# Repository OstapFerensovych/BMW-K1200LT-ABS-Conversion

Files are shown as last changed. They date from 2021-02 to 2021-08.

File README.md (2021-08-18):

# BMW K1200LT iABS to iABS gen 2 Conversion PCB and Firmware.

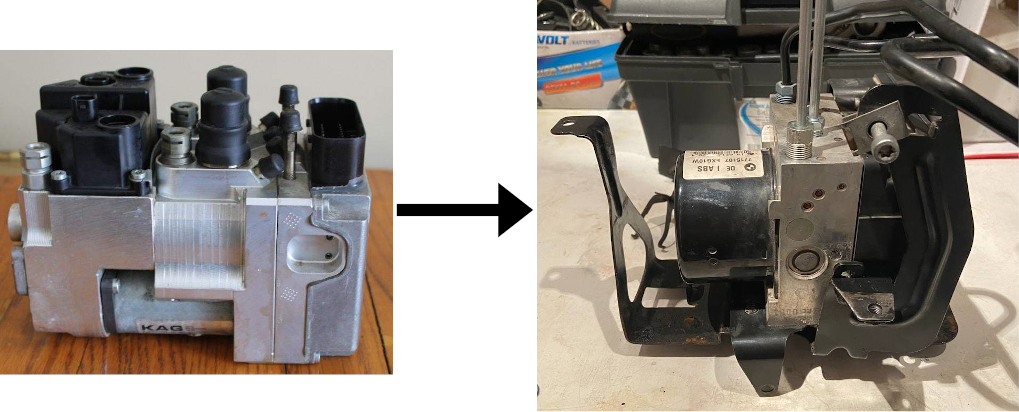
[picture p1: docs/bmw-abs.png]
BMW K1200LT ABS Conversion


To retrofit BMW K1200LT motorcycle we used the ATE/Teves iABS-II module from 2010 R1200GS K25.  
iABS-II uses CAN bus to communicate with ZFE, DME modules in the original R1200GS schematic.  

This project is developed to provide K1200LT necessary signals from ATE/Teves iABS-II CAN bus:
- Speed signal for K1200LT dash
- Brake and tail lights output
- ABS warning LED output
- General warning LED output  

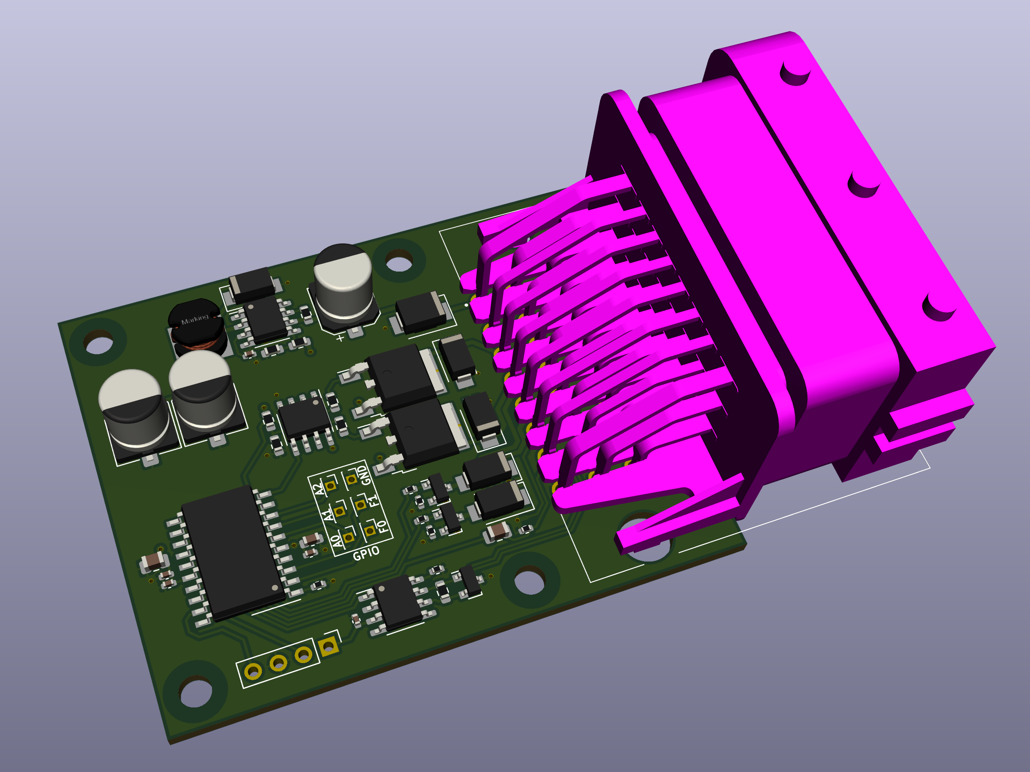
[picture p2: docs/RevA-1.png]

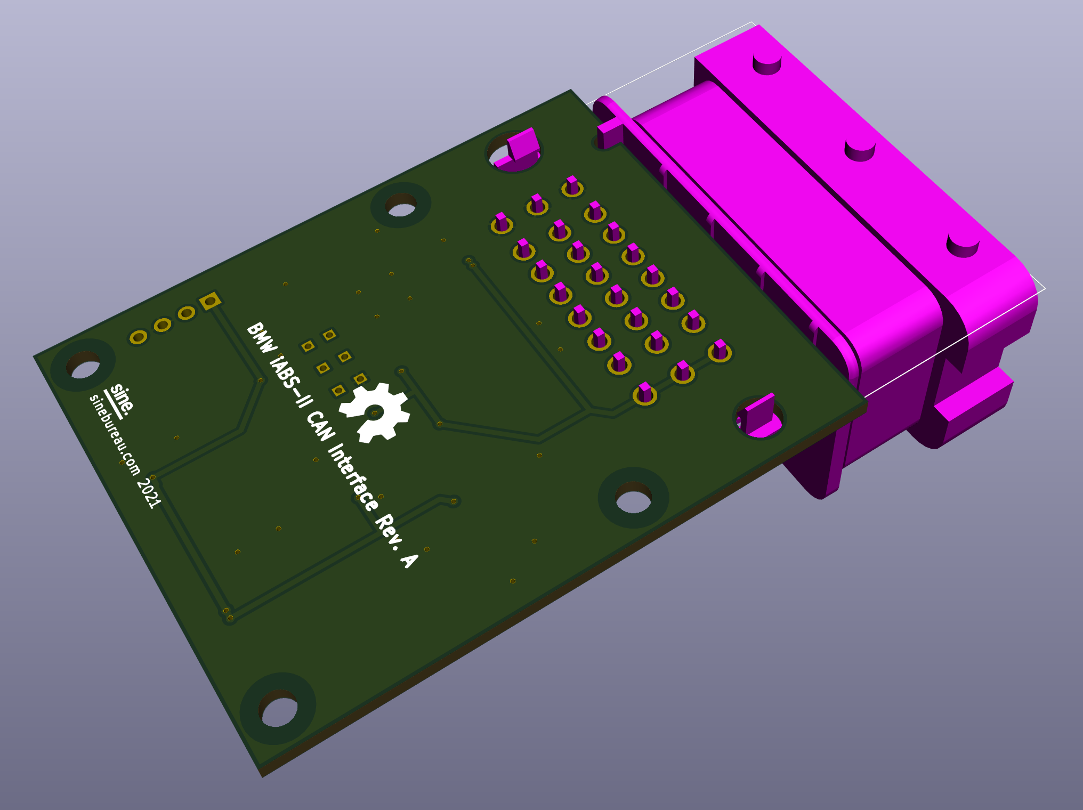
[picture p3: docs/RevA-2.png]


<!-- ![IMG_1473](https://user-images.githubusercontent.com/11366067/129911985-b8ce3c54-3990-48e8-b734-4c0b1e120d9e.jpg)
![IMG_1475](https://user-images.githubusercontent.com/11366067/129912004-15128995-6d64-4012-b580-ba468f006576.jpg)
![IMG_1476](https://user-images.githubusercontent.com/11366067/129912034-00b8ea57-16d7-4200-b9ce-d0883e993687.jpg) -->


## Other resources. 
[Shematics](docs/)

#### PCB is designed in KiCAD 5.1.9

## License

MIT

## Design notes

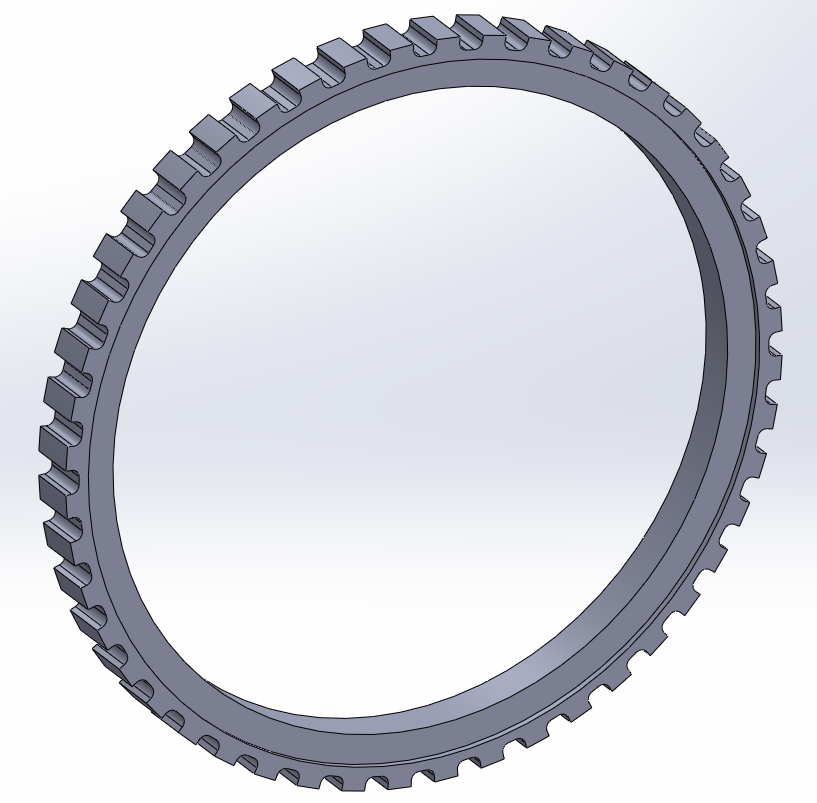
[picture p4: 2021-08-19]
docs/K1200LT_Rear_ABS_ring_48T.png

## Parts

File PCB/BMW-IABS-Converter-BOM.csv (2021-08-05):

Reference(s) | Value | Footprint | Qty | Url
C6 | 10uF | Capacitor_SMD:C_0805_2012Metric | 1
C8 | 47uF 25V | Capacitor_THT:C_Radial_D6.3mm_H11.0mm_P2.50mm | 1
C14 | 150pF | Capacitor_SMD:C_0402_1005Metric | 1 | https://www.rcscomponents.kiev.ua/product/180pf-50v-np0-5-0805-4k-reel-0805n181j500nt-hitano_54905.html
D1, D2, D3, D4 | US1M | Diode_SMD:D_SMA | 4
Q2, Q3 | IRLML0060TRPbF | Package_TO_SOT_SMD:SOT-23 | 2
R1, R7 | 200R | Resistor_SMD:R_0603_1608Metric | 2
R8, R10 | 20K | Resistor_SMD:R_0603_1608Metric | 2
R9 | 10K | Resistor_SMD:R_1206_3216Metric | 1
R11 | 2K | Resistor_SMD:R_1206_3216Metric | 1
R13 | 120R | Resistor_SMD:R_0603_1608Metric | 1
R19 | 3K 1% | Resistor_SMD:R_0603_1608Metric | 1 | https://www.rcscomponents.kiev.ua/product/3-32-kohm-1-0-125w-150v-0805-rc0805fr-3k32-hitano-rezistor-smd_27756.html
U2 | STM32F042F4Px | Package_SO:TSSOP-20_4.4x6.5mm_P0.65mm | 1
U3 | LMC662AIM | Package_SO:SOIC-8_3.9x4.9mm_P1.27mm | 1

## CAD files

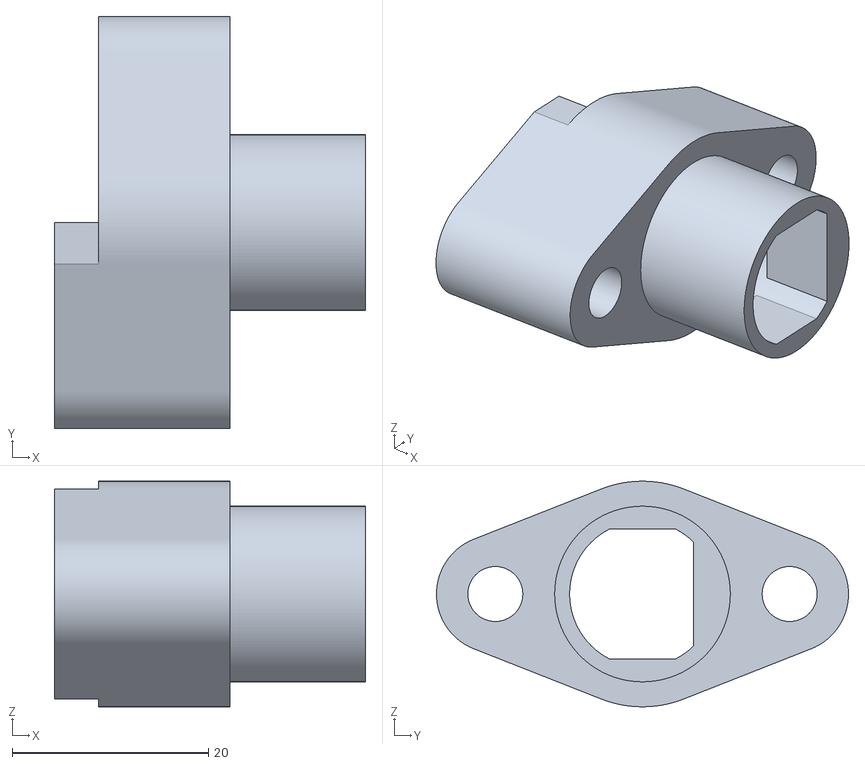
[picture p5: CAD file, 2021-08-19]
3D Files/K1200LT_ABS_Sensor_Bracket.stl
31.7 x 42.0 x 23.0

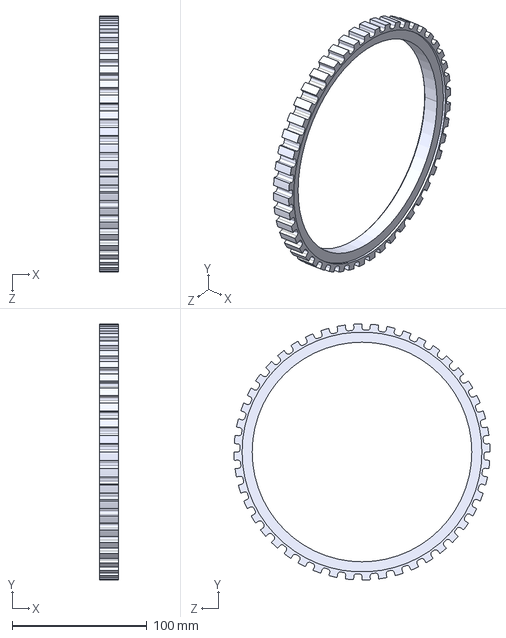
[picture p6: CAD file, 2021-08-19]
3D Files/K1200LT-Rear-ABS-Ring-48T.STEP
14.0 x 190.0 x 190.0 mm

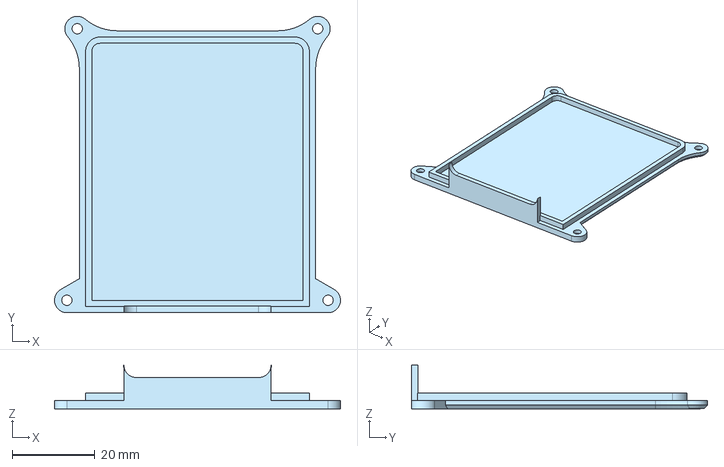
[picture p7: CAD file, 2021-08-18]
3D Files/Case-02a.step
69.0 x 71.5 x 10.6 mm

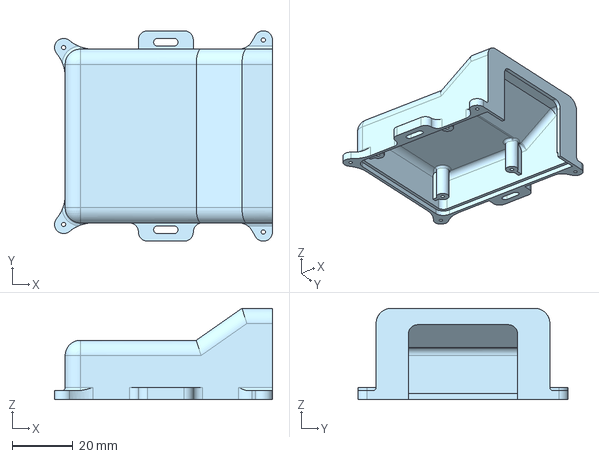
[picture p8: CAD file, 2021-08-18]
3D Files/Case-01a.step
71.5 x 69.0 x 30.0 mm

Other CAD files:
3D Files/Case-02a.stl

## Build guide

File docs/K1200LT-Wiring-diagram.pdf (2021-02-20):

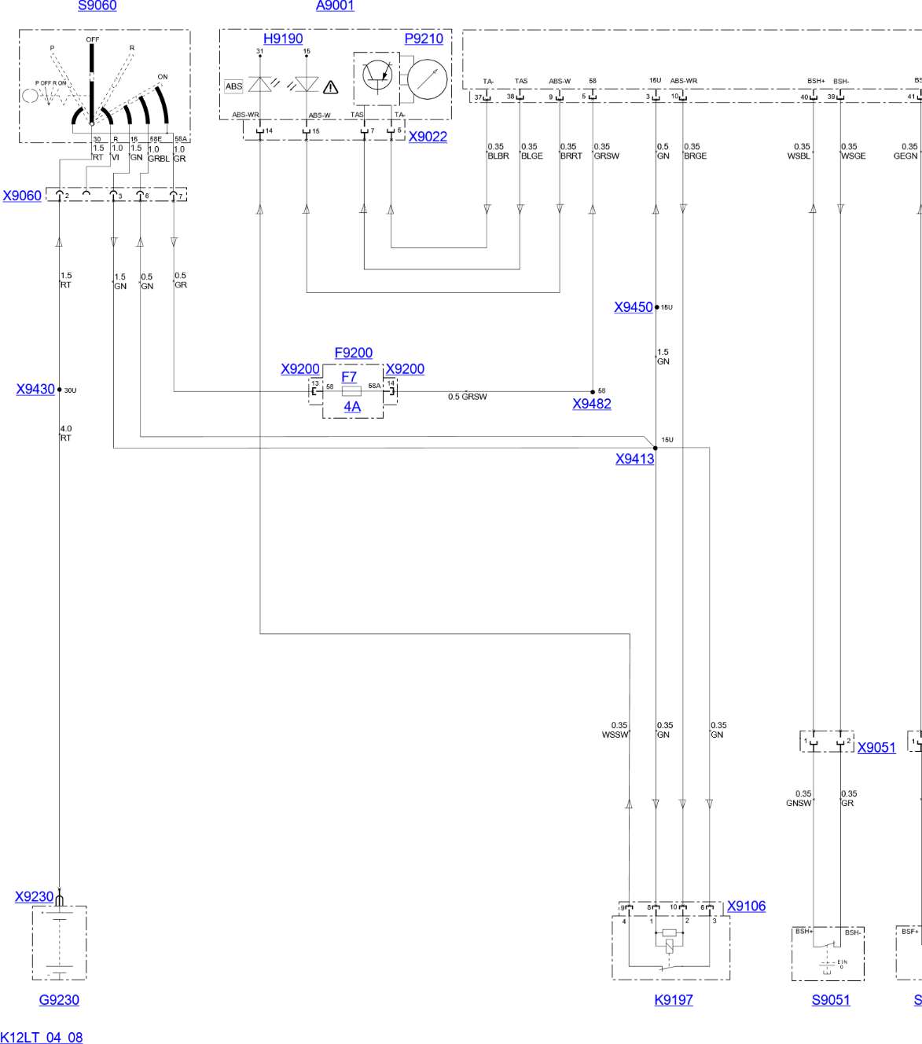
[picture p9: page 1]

SSP-SSP-BIKE_K12LT_04_08 BIKE_K12LT_04_08 | 1/3

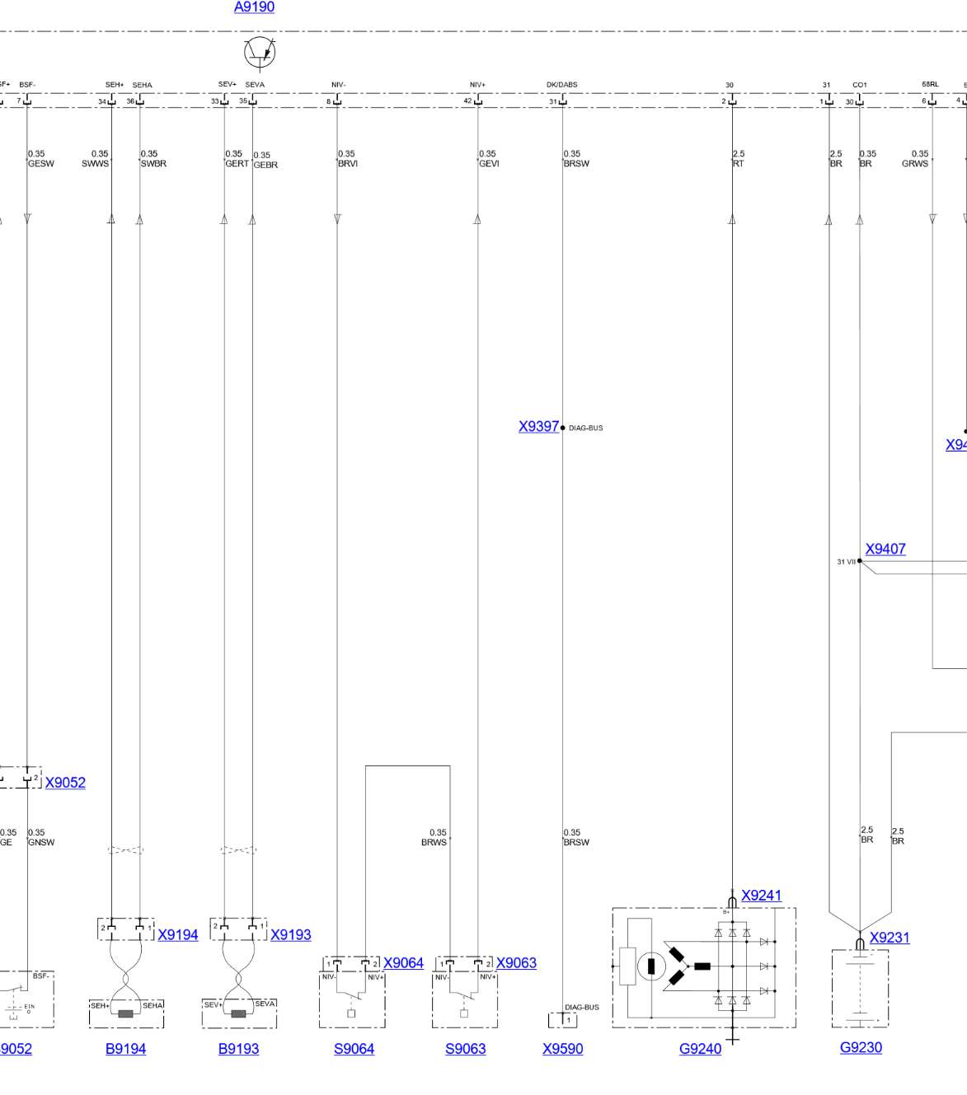
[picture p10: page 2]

SSP-SSP-BIKE_K12LT_04_08 BIKE_K12LT_04_08 | 2/3

SSP-SSP-BIKE_K12LT_04_08 BIKE_K12LT_04_08 | 3/3

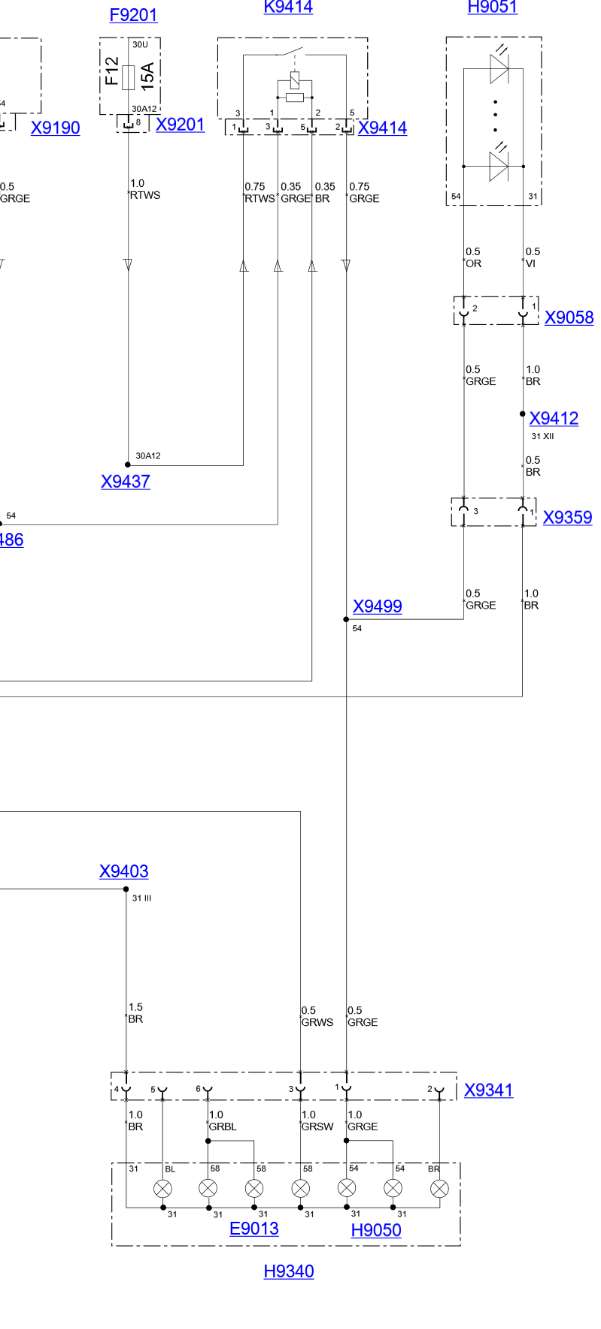
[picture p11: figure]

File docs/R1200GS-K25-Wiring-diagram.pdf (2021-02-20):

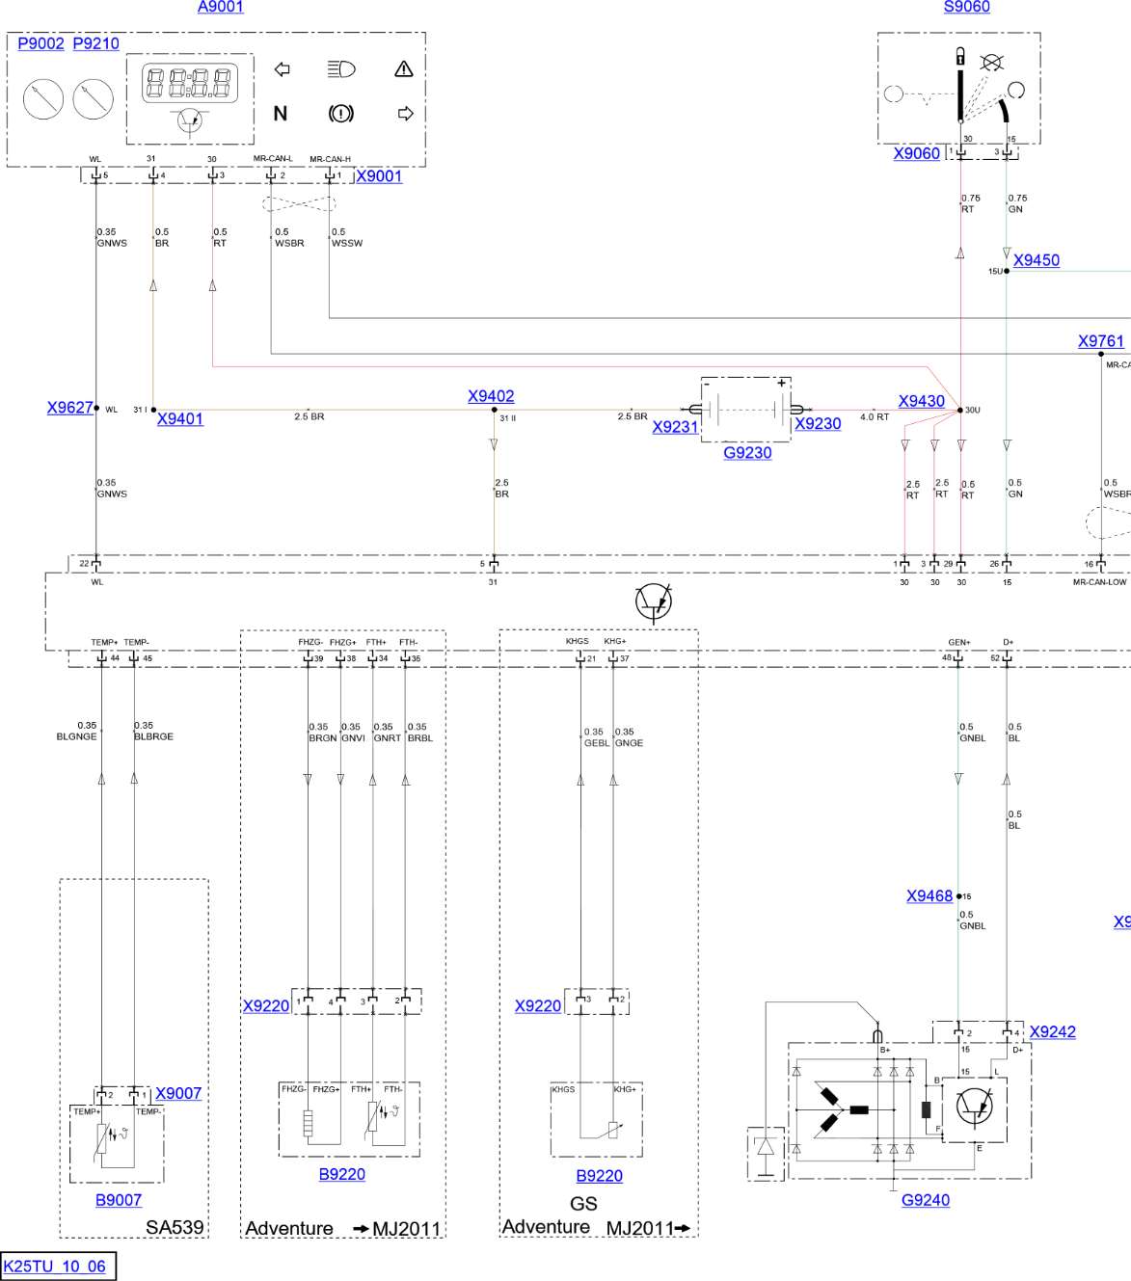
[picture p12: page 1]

SSP-SSP-BIKE_K25TU_10_06 BIKE_K25TU_10_06 | 1/3

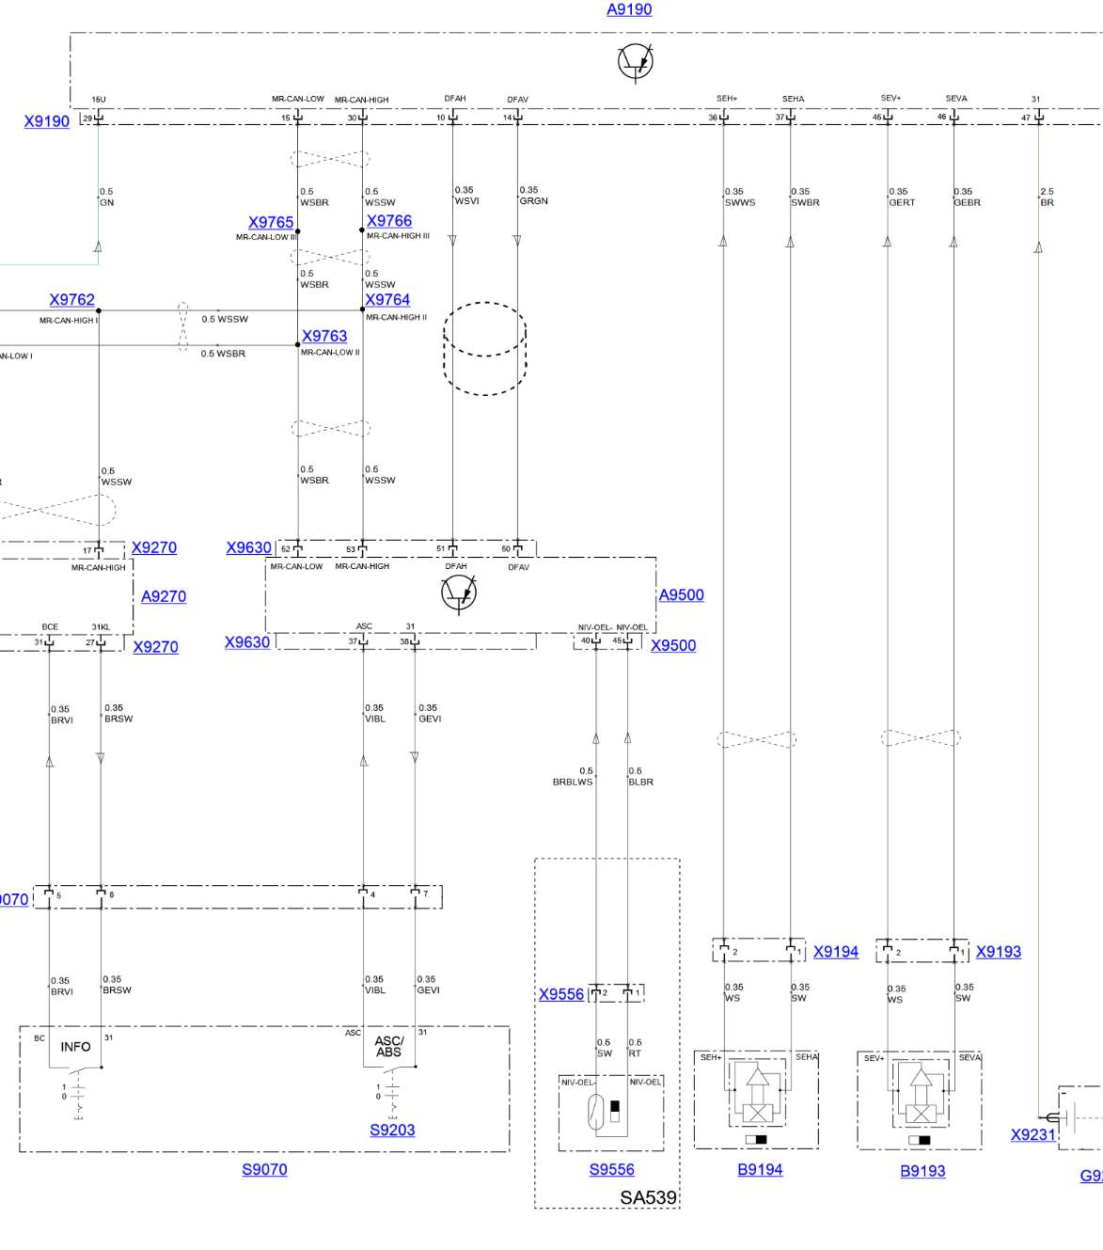
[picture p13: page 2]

SSP-SSP-BIKE_K25TU_10_06 BIKE_K25TU_10_06 | 2/3

SSP-SSP-BIKE_K25TU_10_06 BIKE_K25TU_10_06 | 3/3

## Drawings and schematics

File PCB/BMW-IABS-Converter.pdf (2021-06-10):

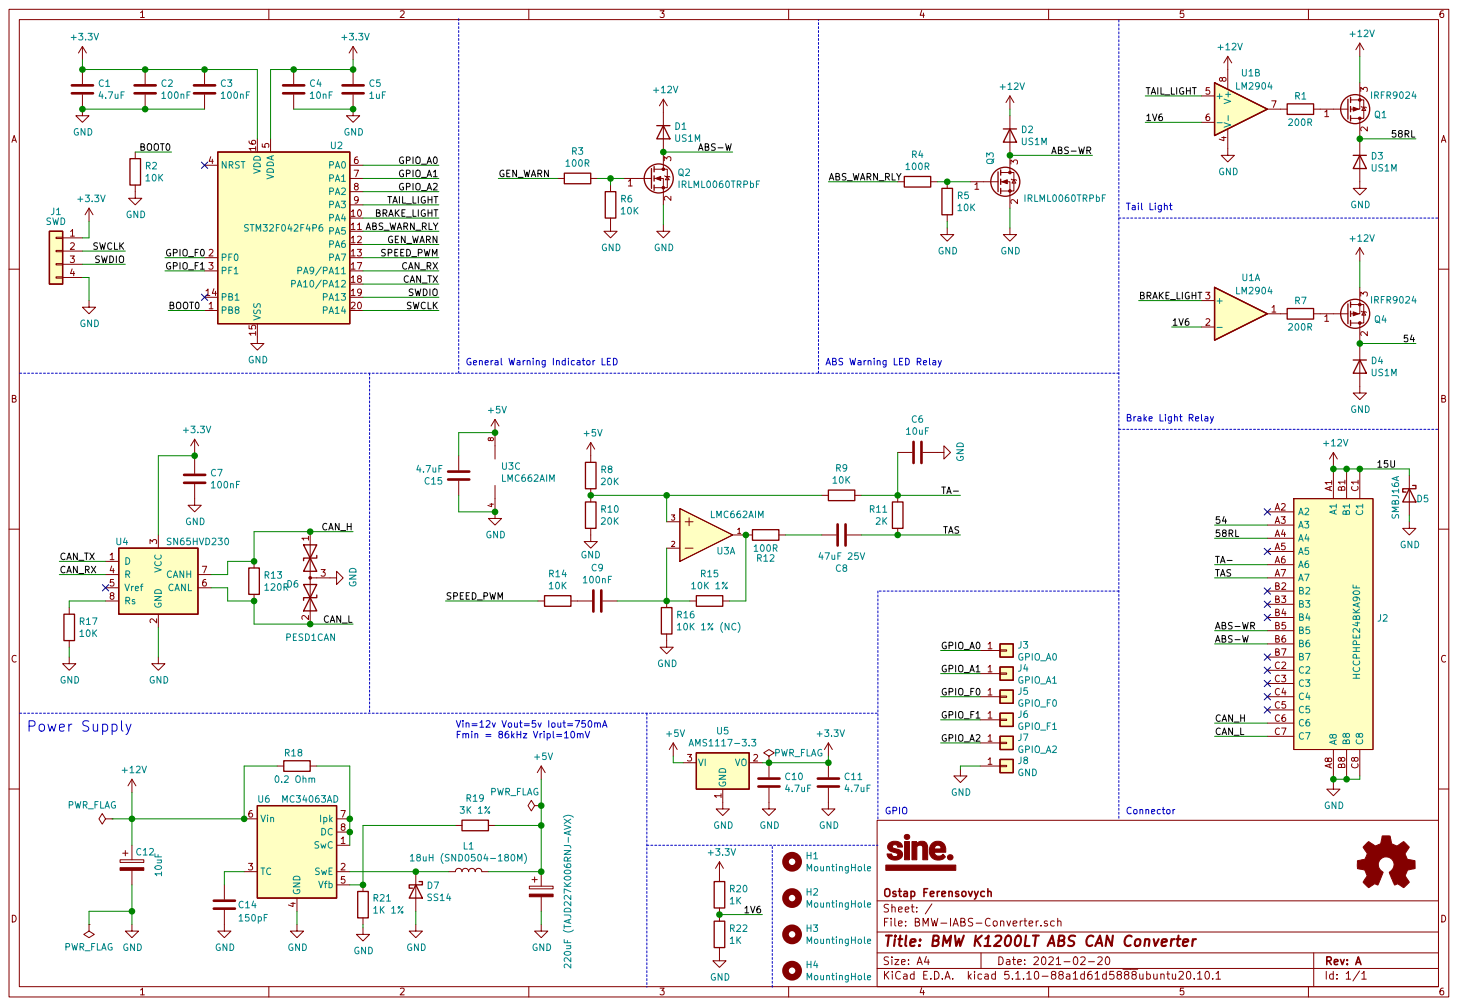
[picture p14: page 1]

Connector General Warning Indicator LED

ABS Warning LED Relay

Id: 1/1 Title: BMW K1200LT ABS CAN Converter File: BMW-IABS-Converter.sch Sheet: / Ostap Ferensovych

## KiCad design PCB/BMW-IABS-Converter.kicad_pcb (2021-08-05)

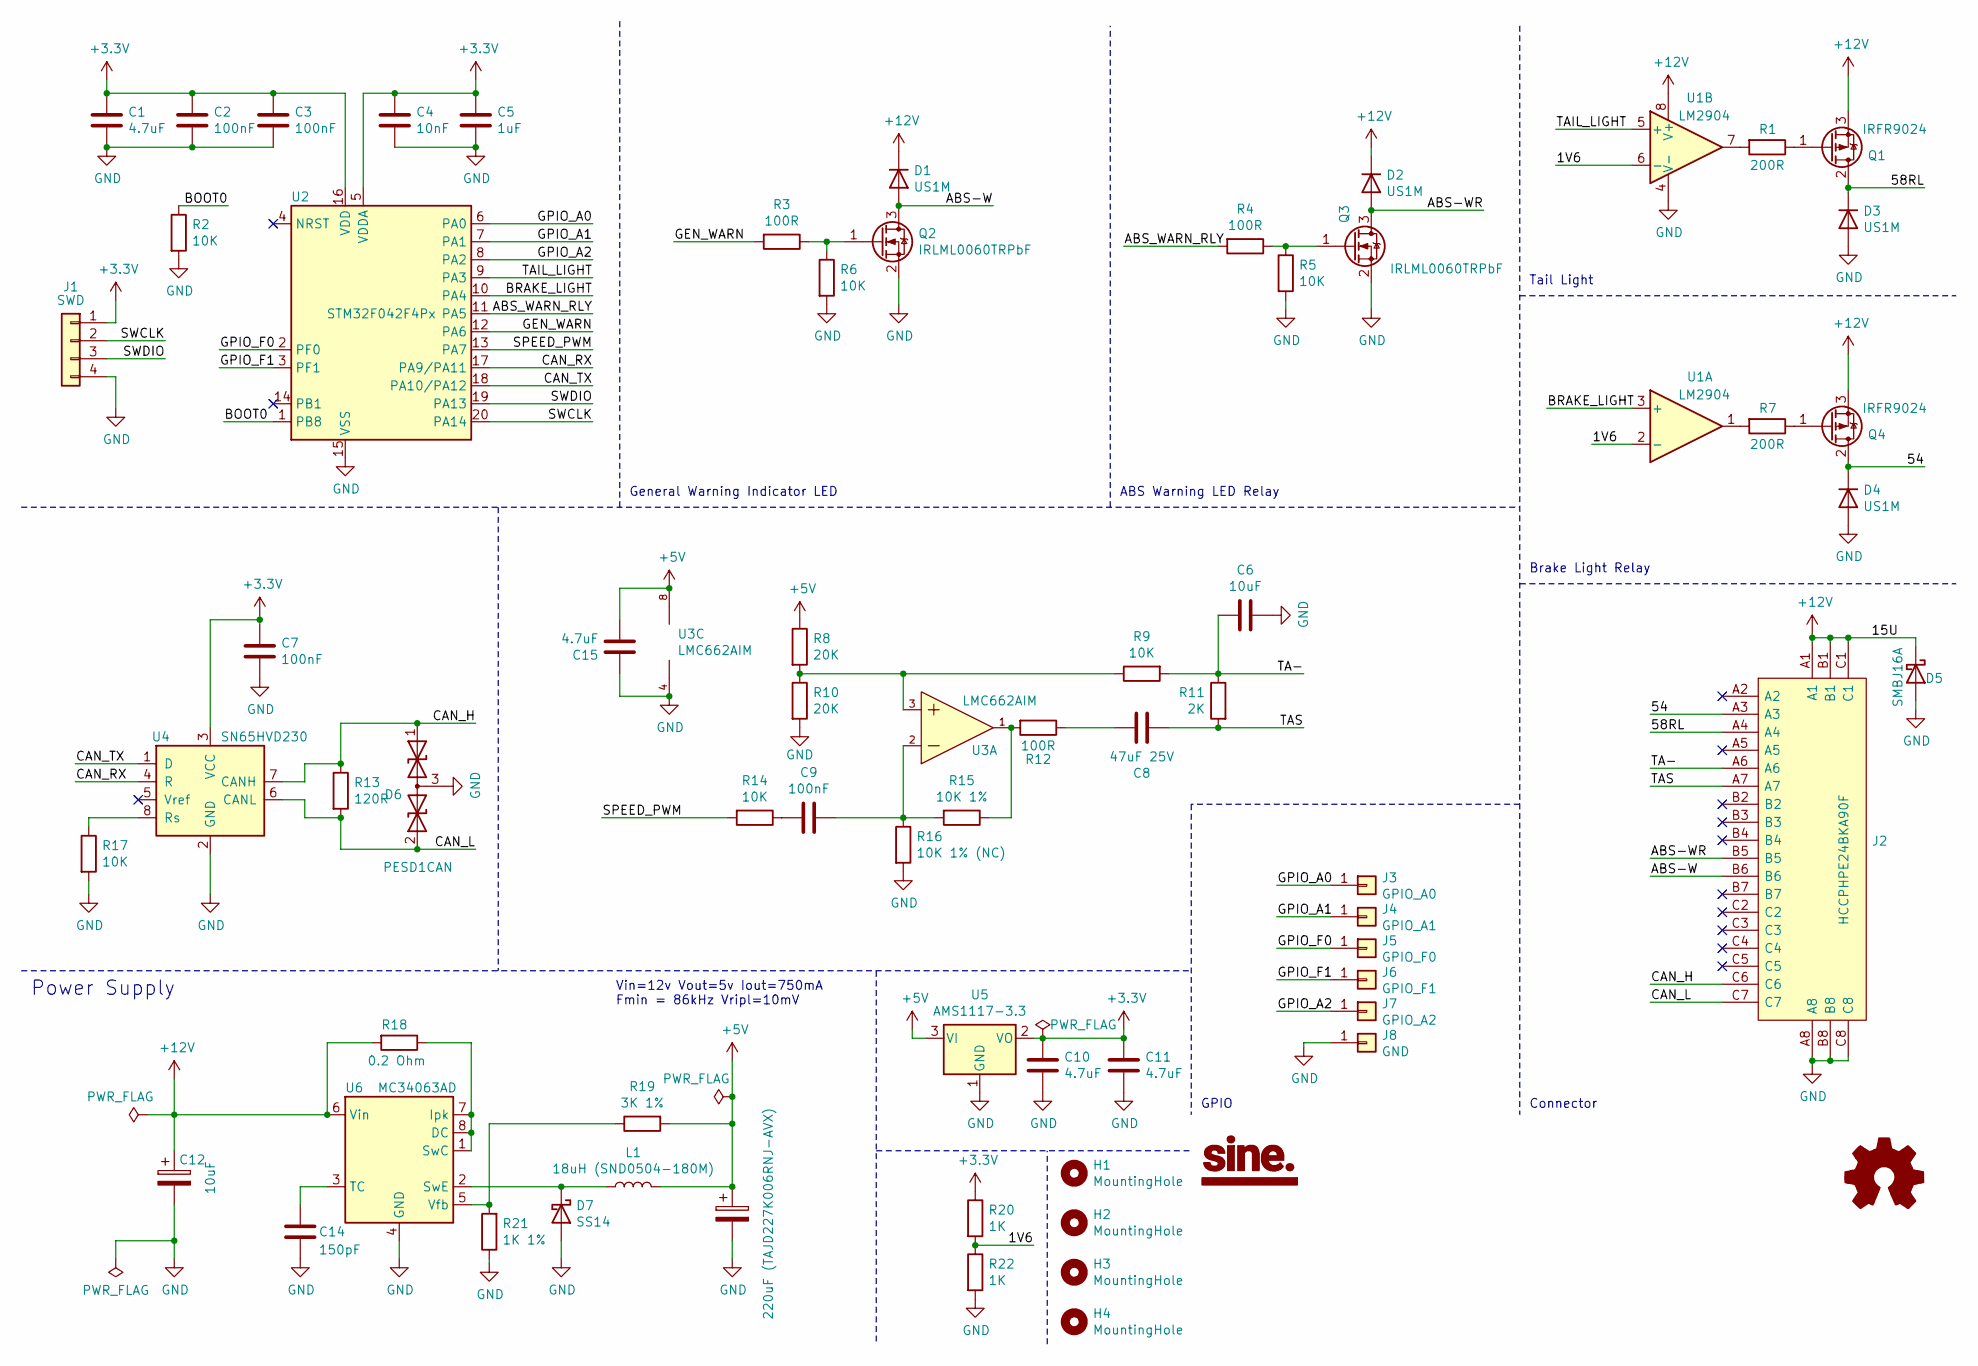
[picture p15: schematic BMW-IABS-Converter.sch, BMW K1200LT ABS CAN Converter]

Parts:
C1, C10, C11, C15: 4.7uF; C_0805_2012Metric
C2, C3, C7, C9: 100nF; C_0402_1005Metric
C4: 10nF; C_0402_1005Metric
C5: 1uF; C_0603_1608Metric
C6: 10uF; C_0805_2012Metric
C8: 47uF 25V; C_Radial_D6.3mm_H11.0mm_P2.50mm
C12: 10uF; C_1206_3216Metric
C13: 220uF (TAJD227K006RNJ-AVX); CP_EIA-7343-31_Kemet-D
C14: 150pF; C_0402_1005Metric
D1, D2, D3, D4: US1M; D_SMA
D5: SMBJ16A; D_SMB
D6: PESD1CAN; SOT-23
D7: SS14; D_SMA
H1, H2, H3, H4: MountingHole; MountingHole_3.2mm_M3
J1: SWD; PinHeader_1x04_P2.54mm_Vertical
J2: HCCPHPE24BKA90F; Manufacturer_Part_Number HCCPHPE24BKA90F
J3: GPIO_A0; PinHeader_1x01_P1.27mm_Vertical
J4: GPIO_A1; PinHeader_1x01_P1.27mm_Vertical
J5: GPIO_F0; PinHeader_1x01_P1.27mm_Vertical
J6: GPIO_F1; PinHeader_1x01_P1.27mm_Vertical
J7: GPIO_A2; PinHeader_1x01_P1.27mm_Vertical
J8: GND; PinHeader_1x01_P1.27mm_Vertical
L1: 18uH (SND0504-180M); L_Wuerth_WE-PD2-Typ-MS
LOGO1: Sine_Logo_S; sine_logo_small
LOGO2: Logo_Open_Hardware_Small; OSHW-Symbol_6.7x6mm_SilkScreen
Q1, Q4: IRFR9024; TO-252-2
Q2, Q3: IRLML0060TRPbF; SOT-23
R1, R7: 200R; R_0603_1608Metric
R2, R5, R6, R14, R17: 10K; R_0402_1005Metric
R3, R4, R12: 100R; R_0402_1005Metric
R8, R10: 20K; R_0603_1608Metric
R9: 10K; R_1206_3216Metric
R11: 2K; R_1206_3216Metric
R13: 120R; R_0603_1608Metric
R15: 10K 1%; R_0402_1005Metric
R16: 10K 1% (NC); R_0402_1005Metric
R18: 0.2 Ohm; R_0603_1608Metric
R19: 3K 1%; R_0603_1608Metric
R20, R22: 1K; R_0805_2012Metric
R21: 1K 1%; R_0603_1608Metric
U1: LM2904; SOIC-8_3.9x4.9mm_P1.27mm
U2: STM32F042F4Px; TSSOP-20_4.4x6.5mm_P0.65mm
U3: LMC662AIM; SOIC-8_3.9x4.9mm_P1.27mm
U4: SN65HVD230; SOIC-8_3.9x4.9mm_P1.27mm
U5: AMS1117-3.3; SOT-223-3_TabPin2
U6: MC34063AD; SOIC-8_3.9x4.9mm_P1.27mm

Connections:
+3V3: C1.1, C2.1, C3.1, C4.1, C5.1, C7.1, C10.1, C11.1, J1.1, R20.1, U2.5 (VDDA), U2.16 (VDD), U4.3 (VCC), U5.2 (VO)
+5V: C13.1, C15.2, L1.2, R8.1, R19.2, U3.8 (V+), U5.3 (VI)
+12V: C12.1, D1.1 (K), D2.1 (K), D5.1 (K), J2.A1, J2.B1, J2.C1, Q1.3 (S), Q4.3 (S), R18.2, U1.8 (V+), U6.6 (Vin)
/1V6: R20.2, R22.1, U1.2 (-), U1.6 (-)
/54: D4.1 (K), J2.A3, Q4.2 (D)
/58RL: D3.1 (K), J2.A4, Q1.2 (D)
/ABS-W: D1.2 (A), J2.B6, Q2.3 (D)
/ABS-WR: D2.2 (A), J2.B5, Q3.3 (D)
/ABS_WARN_RLY: R4.2, U2.11 (PA5)
/BOOT0: R2.1, U2.1 (PB8)
/BRAKE_LIGHT: U1.3 (+), U2.10 (PA4)
/CAN_H: D6.1 (A1), J2.C6, R13.1, U4.7 (CANH)
/CAN_L: D6.2 (A2), J2.C7, R13.2, U4.6 (CANL)
/CAN_RX: U2.17 (PA9/PA11), U4.4 (R)
/CAN_TX: U2.18 (PA10/PA12), U4.1 (D)
/GEN_WARN: R3.2, U2.12 (PA6)
/GPIO_A0: J3.1, U2.6 (PA0)
/GPIO_A1: J4.1, U2.7 (PA1)
/GPIO_A2: J7.1, U2.8 (PA2)
/GPIO_F0: J5.1, U2.2 (PF0)
/GPIO_F1: J6.1, U2.3 (PF1)
/SPEED_PWM: R14.2, U2.13 (PA7)
/SWCLK: J1.2, U2.20 (PA14)
/SWDIO: J1.3, U2.19 (PA13)
/TA-: C6.2, J2.A6, R9.2, R11.1
/TAIL_LIGHT: U1.5 (+), U2.9 (PA3)
/TAS: C8.1, J2.A7, R11.2
GND: C1.2, C2.2, C3.2, C4.2, C5.2, C6.1, C7.2, C10.2, C11.2, C12.2, C13.2, C14.2, C15.1, D3.2 (A), D4.2 (A), D5.2 (A), D6.3 (common), D7.2 (A), J1.4, J2.A8, J2.B8, J2.C8, J8.1, Q2.2 (S), Q3.2 (S), R2.2, R5.2, R6.2, R10.2, R16.2, R17.2, R21.1, R22.2, U1.4 (V-), U2.15 (VSS), U3.4 (V-), U4.2 (GND), U5.1 (GND), U6.4 (GND)
unnamed: C8.2, R12.1
unnamed: C9.1, R15.2, R16.1, U3.2 (INA-)
unnamed: C9.2, R14.1
unnamed: C14.1, U6.3 (TC)
unnamed: D7.1 (K), L1.1, U6.2 (SwE)
unnamed: Q1.1 (G), R1.1
unnamed: Q2.1 (G), R3.1, R6.1
unnamed: Q3.1 (G), R4.1, R5.1
unnamed: Q4.1 (G), R7.1
unnamed: R1.2, U1.7
unnamed: R7.2, U1.1
unnamed: R8.2, R9.1, R10.1, U3.3 (INA+)
unnamed: R12.2, R15.1, U3.1 (OUTA)
unnamed: R17.1, U4.8 (Rs)
unnamed: R18.1, U6.1 (SwC), U6.7 (Ipk), U6.8 (DC)
unnamed: R19.1, R21.2, U6.5 (Vfb)

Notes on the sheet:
Power Supply
Vin=12v Vout=5v Iout=750mA Fmin = 86kHz Vripl=10mV
ABS Warning LED Relay
General Warning Indicator LED
Brake Light Relay
Tail Light
Connector
GPIO

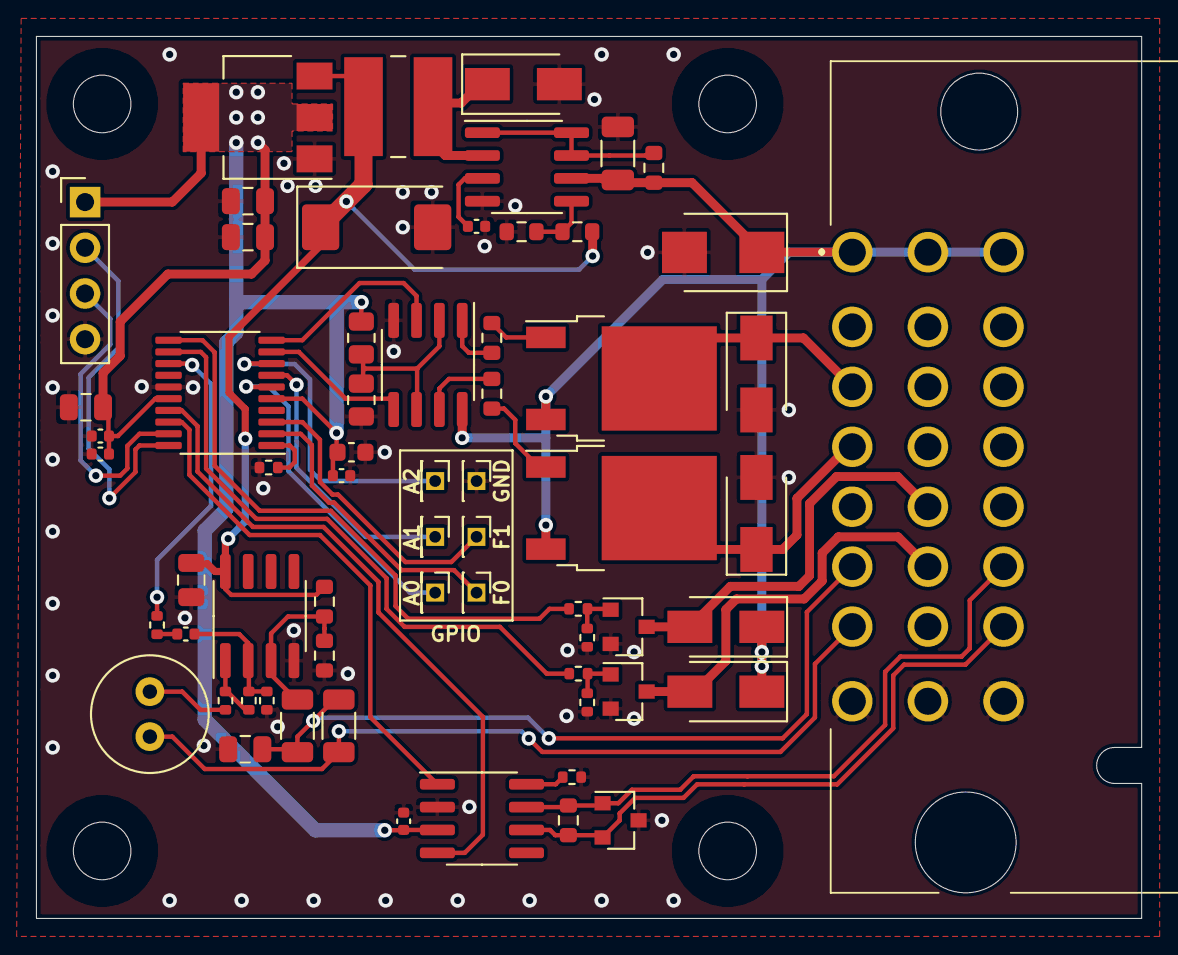
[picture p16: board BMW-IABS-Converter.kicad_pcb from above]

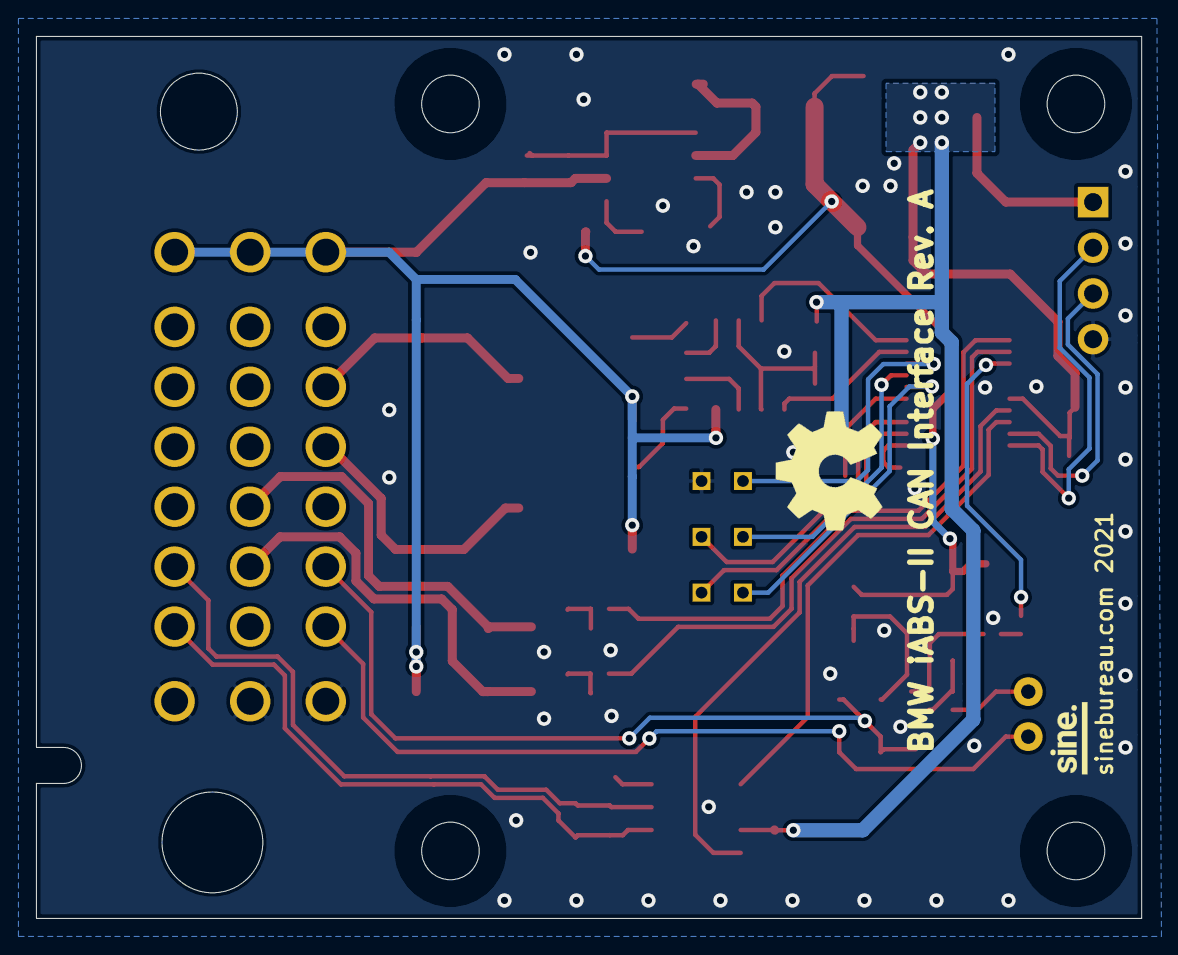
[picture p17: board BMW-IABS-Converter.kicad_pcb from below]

Board: 2 copper layers, 61.4 x 49.0 mm, 69 parts (2 on the bottom side), 44 nets.

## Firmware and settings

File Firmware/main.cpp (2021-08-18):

#include "errors.hpp"
#include "gpio.hpp"
#include "rcc.h"
#include "stm32f0xx.h"
#include "timing.hpp"
#include "can.hpp"
#include "speedo.hpp"

[[noreturn]] int main();
[[noreturn]] int main() {
    rcc_init();
    errors_init();
    timing_init();

    SET_BIT(RCC->APB2ENR, RCC_APB2ENR_SYSCFGCOMPEN);
    READ_BIT(RCC->APB2ENR, RCC_APB2ENR_SYSCFGCOMPEN);
    SET_BIT(SYSCFG->CFGR1, SYSCFG_CFGR1_PA11_PA12_RMP);

    gpio::init();
    timing_sleep_ms(1000);

    gpio::clear<gpio::line::tail_lights>(); //Turn on Tail lights.

    CAN_Init();
    SPEEDO_Init();

    for (;;){
        if(CAN_front_lever() || CAN_rear_lever()) {
            gpio::clear<gpio::line::brake_lights>();
        } else {
            gpio::set<gpio::line::brake_lights>();
        }

        if(CAN_front_sensor_ok() && CAN_rear_sensor_ok()) {
            gpio::clear<gpio::line::abs_warn_relay>();
        } else {
            gpio::set<gpio::line::abs_warn_relay>();
        }

        if(CAN_abs_on()) {
            gpio::set<gpio::line::gen_warn>();
        } else {
            gpio::clear<gpio::line::gen_warn>();
        }

        SPEEDO_Out(CAN_SpeedRearWheel());
    }
}

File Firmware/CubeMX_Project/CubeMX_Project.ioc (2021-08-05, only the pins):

Mcu.UserName=STM32F042F4Px
PA0.Signal=GPIO_Output
PA1.Signal=GPIO_Output
PA11.Signal=CAN_RX
PA12.Signal=CAN_TX
PA13.Signal=SYS_SWDIO
PA14.Signal=SYS_SWCLK
PA2.Signal=GPIO_Output
PA3.GPIO_Label=Tail_light
PA3.Signal=GPIO_Output
PA4.GPIO_Label=Brake_light
PA4.Signal=GPIO_Output
PA5.GPIO_Label=ABS_Warn_RLY
PA5.Signal=GPIO_Output
PA6.GPIO_Label=Gen_warn
PA6.Signal=GPIO_Output
PA7.GPIO_Label=Speedo
PA7.Signal=S_TIM3_CH2
PF0-OSC_IN.Signal=GPIO_Output
PF1-OSC_OUT.Signal=GPIO_Output

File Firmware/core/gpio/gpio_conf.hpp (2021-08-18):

#pragma once
#include "gpio.hpp"

enum class line {
    __invalid__,
    can_rx,
    can_tx,
    speedo,
    gen_warn,
    abs_warn_relay,
    brake_lights,
    tail_lights,
    gpio_A0,
    gpio_A1,
    gpio_A2,
    gpio_F0,
    gpio_F1
};

// clang-format off
constexpr std::pair<line, gpio::pin_config> pins_config[] = {
    {line::can_rx,         {gpio::port::a, 11, 0, gpio::mode::af_io, gpio::drive::push_pull, gpio::speed::high, gpio::pull::none, gpio::alt_func::af4}},
    {line::can_tx,         {gpio::port::a, 12, 0, gpio::mode::af_io, gpio::drive::push_pull, gpio::speed::high, gpio::pull::none, gpio::alt_func::af4}},
    {line::speedo,         {gpio::port::a, 7, 0,  gpio::mode::af_io,  gpio::drive::push_pull, gpio::speed::high, gpio::pull::none, gpio::alt_func::af1 }},
    {line::gen_warn,       {gpio::port::a, 6, 0,  gpio::mode::gp_out,  gpio::drive::push_pull, gpio::speed::low, gpio::pull::none, gpio::alt_func::none }},
    {line::abs_warn_relay, {gpio::port::a, 5, 1,  gpio::mode::gp_out,  gpio::drive::push_pull, gpio::speed::low, gpio::pull::none, gpio::alt_func::none }},
    {line::brake_lights,   {gpio::port::a, 4, 1,  gpio::mode::gp_out,  gpio::drive::push_pull, gpio::speed::low, gpio::pull::none, gpio::alt_func::none }},
    {line::tail_lights,    {gpio::port::a, 3, 1,  gpio::mode::gp_out,  gpio::drive::push_pull, gpio::speed::low, gpio::pull::none, gpio::alt_func::none }},
    {line::gpio_A0,        {gpio::port::a, 0, 0,  gpio::mode::gp_out,  gpio::drive::push_pull, gpio::speed::low, gpio::pull::none, gpio::alt_func::none }},
    {line::gpio_A1,        {gpio::port::a, 1, 0,  gpio::mode::gp_out,  gpio::drive::push_pull, gpio::speed::low, gpio::pull::none, gpio::alt_func::none }},
    {line::gpio_A2,        {gpio::port::a, 2, 0,  gpio::mode::gp_out,  gpio::drive::push_pull, gpio::speed::low, gpio::pull::none, gpio::alt_func::none }},
    {line::gpio_F0,        {gpio::port::f, 0, 0,  gpio::mode::gp_out,  gpio::drive::push_pull, gpio::speed::low, gpio::pull::none, gpio::alt_func::none }},
    {line::gpio_F1,        {gpio::port::f, 1, 0,  gpio::mode::gp_out,  gpio::drive::push_pull, gpio::speed::low, gpio::pull::none, gpio::alt_func::none }},
};
// clang-format on

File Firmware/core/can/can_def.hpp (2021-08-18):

#pragma once

const uint16_t can_id_abs_status = 0x294;
const uint16_t can_id_abs_rear_status = 0x2A8;

#define CAN_ABS_STATUS_Pos (12U)
#define CAN_ABS_STATUS_Msk (0xF000)

#define CAN_FR_SENSOR_OK_Pos (0U+48U)
#define CAN_FR_SENSOR_OK_Msk (0x1000000000000)
#define CAN_RR_SENSOR_OK_Pos (1U+48U)
#define CAN_RR_SENSOR_OK_Msk (0x2000000000000)

#define CAN_FR_LEVR_Pos  (2U+48U)
#define CAN_FR_LEVR_Msk  (0x4000000000000)
#define CAN_RR_LEVR_Pos  (3U+48U)
#define CAN_RR_LEVR_Msk  (0x8000000000000)

#define CAN_FRONT_SPEED_Pos           (16U)
#define CAN_FRONT_SPEED_Msk           (0xFFFF0000)

#define CAN_REAR_SPEED_Pos           (16U)
#define CAN_REAR_SPEED_Msk           (0xFFFF0000)

/* bxCAN Related */
#define CAN_INIT_MODE_TMO 10

#define CAN_MODE_NORMAL             (0x00000000U)                              /*!< Normal mode   */
#define CAN_MODE_LOOPBACK           ((uint32_t)CAN_BTR_LBKM)                   /*!< Loopback mode */
#define CAN_MODE_SILENT             ((uint32_t)CAN_BTR_SILM)                   /*!< Silent mode   */
#define CAN_MODE_SILENT_LOOPBACK    ((uint32_t)(CAN_BTR_LBKM | CAN_BTR_SILM))  /*!< Loopback combined with silent mode */

#define CAN_SJW_1TQ                 (0x00000000U)              /*!< 1 time quantum */
#define CAN_SJW_2TQ                 ((uint32_t)CAN_BTR_SJW_0)  /*!< 2 time quantum */
#define CAN_SJW_3TQ                 ((uint32_t)CAN_BTR_SJW_1)  /*!< 3 time quantum */
#define CAN_SJW_4TQ                 ((uint32_t)CAN_BTR_SJW)    /*!< 4 time quantum */

#define CAN_BS1_1TQ                 (0x00000000U)                                                /*!< 1 time quantum  */
#define CAN_BS1_2TQ                 ((uint32_t)CAN_BTR_TS1_0)                                    /*!< 2 time quantum  */
#define CAN_BS1_3TQ                 ((uint32_t)CAN_BTR_TS1_1)                                    /*!< 3 time quantum  */
#define CAN_BS1_4TQ                 ((uint32_t)(CAN_BTR_TS1_1 | CAN_BTR_TS1_0))                  /*!< 4 time quantum  */
#define CAN_BS1_5TQ                 ((uint32_t)CAN_BTR_TS1_2)                                    /*!< 5 time quantum  */
#define CAN_BS1_6TQ                 ((uint32_t)(CAN_BTR_TS1_2 | CAN_BTR_TS1_0))                  /*!< 6 time quantum  */
#define CAN_BS1_7TQ                 ((uint32_t)(CAN_BTR_TS1_2 | CAN_BTR_TS1_1))                  /*!< 7 time quantum  */
#define CAN_BS1_8TQ                 ((uint32_t)(CAN_BTR_TS1_2 | CAN_BTR_TS1_1 | CAN_BTR_TS1_0))  /*!< 8 time quantum  */
#define CAN_BS1_9TQ                 ((uint32_t)CAN_BTR_TS1_3)                                    /*!< 9 time quantum  */
#define CAN_BS1_10TQ                ((uint32_t)(CAN_BTR_TS1_3 | CAN_BTR_TS1_0))                  /*!< 10 time quantum */
#define CAN_BS1_11TQ                ((uint32_t)(CAN_BTR_TS1_3 | CAN_BTR_TS1_1))                  /*!< 11 time quantum */
#define CAN_BS1_12TQ                ((uint32_t)(CAN_BTR_TS1_3 | CAN_BTR_TS1_1 | CAN_BTR_TS1_0))  /*!< 12 time quantum */
#define CAN_BS1_13TQ                ((uint32_t)(CAN_BTR_TS1_3 | CAN_BTR_TS1_2))                  /*!< 13 time quantum */
#define CAN_BS1_14TQ                ((uint32_t)(CAN_BTR_TS1_3 | CAN_BTR_TS1_2 | CAN_BTR_TS1_0))  /*!< 14 time quantum */
#define CAN_BS1_15TQ                ((uint32_t)(CAN_BTR_TS1_3 | CAN_BTR_TS1_2 | CAN_BTR_TS1_1))  /*!< 15 time quantum */
#define CAN_BS1_16TQ                ((uint32_t)CAN_BTR_TS1) /*!< 16 time quantum */

#define CAN_BS2_1TQ                 (0x00000000U)                                /*!< 1 time quantum */
#define CAN_BS2_2TQ                 ((uint32_t)CAN_BTR_TS2_0)                    /*!< 2 time quantum */
#define CAN_BS2_3TQ                 ((uint32_t)CAN_BTR_TS2_1)                    /*!< 3 time quantum */
#define CAN_BS2_4TQ                 ((uint32_t)(CAN_BTR_TS2_1 | CAN_BTR_TS2_0))  /*!< 4 time quantum */
#define CAN_BS2_5TQ                 ((uint32_t)CAN_BTR_TS2_2)                    /*!< 5 time quantum */
#define CAN_BS2_6TQ                 ((uint32_t)(CAN_BTR_TS2_2 | CAN_BTR_TS2_0))  /*!< 6 time quantum */
#define CAN_BS2_7TQ                 ((uint32_t)(CAN_BTR_TS2_2 | CAN_BTR_TS2_1))  /*!< 7 time quantum */
#define CAN_BS2_8TQ                 ((uint32_t)CAN_BTR_TS2)                      /*!< 8 time quantum */

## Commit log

2021-02-20 Added wiring diagrams
2021-02-20 Updated schematics
    [BMW-IABS-Converter.kicad_pcb, BMW-IABS-Converter.sch]
2021-02-20 Fixed schematics
    [BMW-IABS-Converter.sch]
2021-02-20 Added connector footprint and symbol
    [BMW-IABS-Converter.kicad_pcb, BMW-IABS-Converter.sch]
2021-02-21 Added connector 3D model
2021-02-21 Updated footprint and layout
    [BMW-IABS-Converter.kicad_pcb]
2021-02-21 Updated schematic and layout
2021-02-21 Added PCB renders
2021-02-22 Updated coil 3d model
    [BMW-IABS-Converter.kicad_pcb]
2021-02-22 Added pdf version of schematic
2021-02-22 Changed MOSFETS to 0030
    [BMW-IABS-Converter.sch]
2021-02-22 Updated schematic
    [BMW-IABS-Converter.sch]
2021-06-10 Updated the PDF version of schematic
2021-06-29 Fixed mcu package.
    [BMW-IABS-Converter.kicad_pcb, BMW-IABS-Converter.sch]
2021-08-05 Refactoring repository
    [BMW-IABS-Converter-BOM.csv, BMW-IABS-Converter.kicad_pcb, BMW-IABS-Converter.sch]
2021-08-18 Added Case files
    [Case-01a.step, Case-02a.step, Case-02a.stl]
2021-08-19 Added rear ABS ring and ABS sensor bracket files
    [K1200LT-Rear-ABS-Ring-48T.STEP, K1200LT_ABS_Sensor_Bracket.stl]
